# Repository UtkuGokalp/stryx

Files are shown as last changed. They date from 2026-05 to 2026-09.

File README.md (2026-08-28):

# Stryx

Stryx is a 3D printable wheeled robot designed as a platform for embedded software development. It has:
 - A power system that handles multiple power rails
 - An STM32 MCU (Nucleo L432KC) for controlling motors, sensors and potential future hardwares
 - An ultrasonic sensor for detecting obstacles
 - USB Connectivity
 - A modular platform that allows secure mounting
 - Various custom mounts

# Features
 - 3D printable parts (without supports)
 - Rear wheel drive via DC motors
 - Power system for managing different power rails
 - STM32 Nucleo L432KC MCU for real time control
 - Basic obstacle avoidance
 - DSP for removing sensor noises
 - Designed to be built on a mid-size breadboard for ease of prototyping and compactness
 - USB connectivity for universal communication (to be integrated better)

# Pictures
Below are the front, top and bottom views of Stryx.
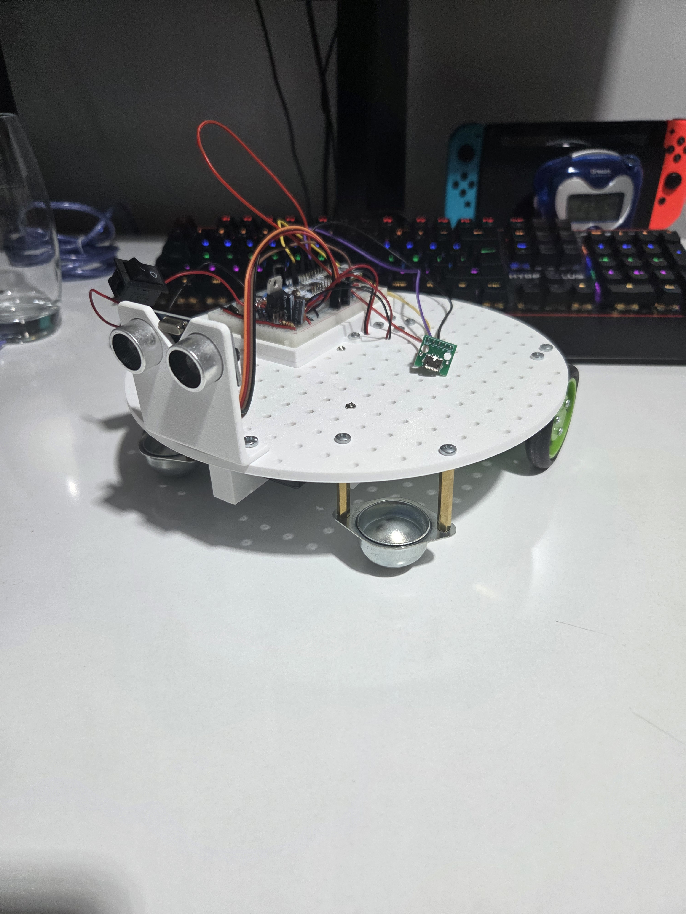
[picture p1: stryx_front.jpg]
Front view of Stryx v1


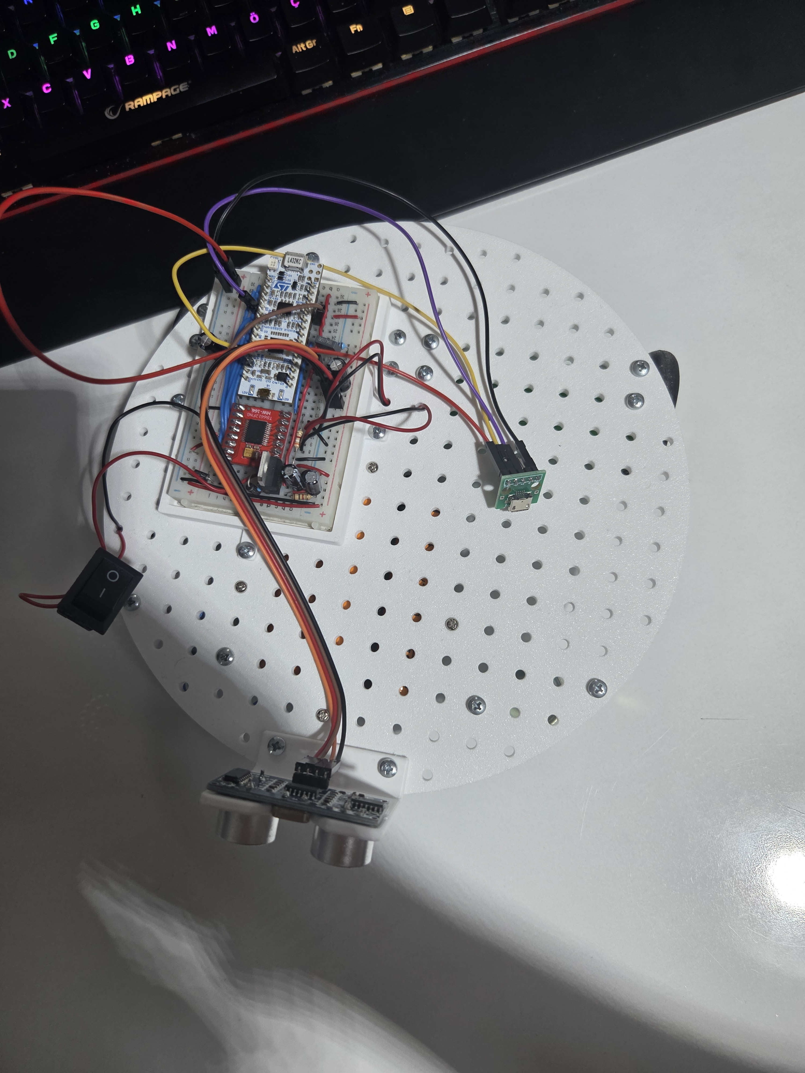
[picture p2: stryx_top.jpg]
Top view of Stryx v1


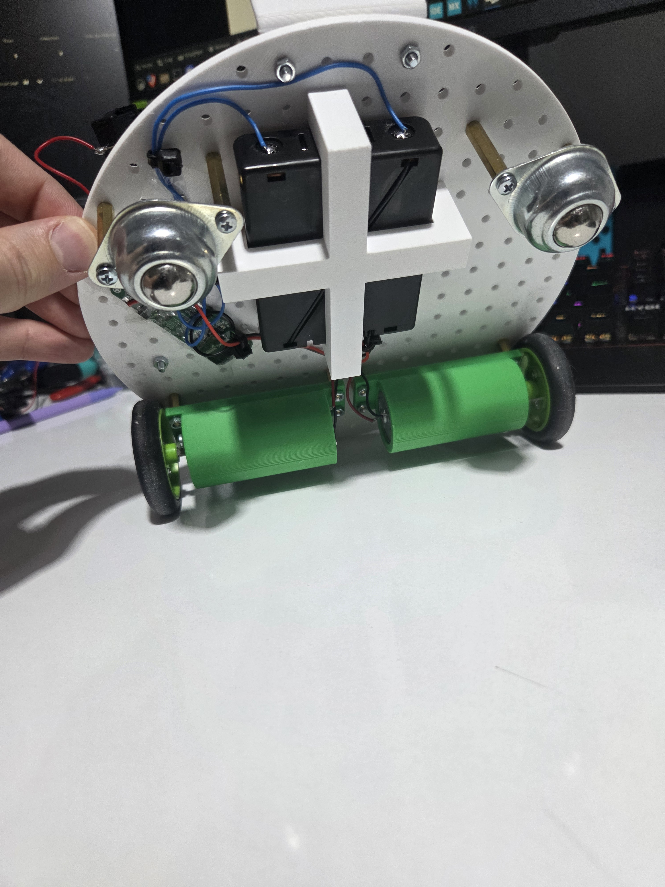
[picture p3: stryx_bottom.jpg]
Bottom view of Stryx v1


# Videos
  - A video of Stryx moving can be viewed [here](https://youtube.com/shorts/t5ViIWTwRgw?feature=share).
  - A video of Stryx detection through the ultrasonic sensor can be viewed [here](https://youtu.be/18g5bbReIh8).
 - Stryx being controlled by a custom controller and avoiding collisions can be viewed [here](https://youtube.com/shorts/JMSHhV6Dkls?si=vsp8z5HZcUrGIarE).

# Roadmap
Current plans to improve this project are in the following order:
 - PCB design
 - Better joystick controls
 - Better sensing of environment with either
   1. More sensors
   2. Servos that control the orientation of sensors
   3. Or sensors that use different technologies such as IR or LiDAR

# Parts List
|Name|Amount|
|-----|-----|
|Mid-size breadboard|1|
|STM32 Nucleo L432KC Dev Board|1|
|USB Micro-B breakout board|1|
|TB6612FNG Module|1|
|12V 250RPM DC Motors|2|
|Omnidirectional Wheels|2|
|LM317T Voltage regulator |1|
|1N4001|3|
|1N5822|1|
|0.1uF ceramic capacitor|2|
|1uF polarized capacitor|1|
|10uF polarized capacitor|1|
|470uF polarized capacitor|2|
|240Ω resistor|1|
|1kΩ resistor|2|
|3.8kΩ resistor|1|
|Neopixel LED Module|1|
|HC-SR04 ultrasonic sensor|1|
|3S 20A BMS|1|
|3200mAh Li-ion batteries|3|
|3S Li-ion battery holder|1|
|Switch (SPDT)|1|
|Screw Terminals|3|
|Rubber Wheels with D-Shaft connections|2|
|M3 screws, nuts, spacers and cables|various amounts|

# Schematic

Schematic is available in `kicad_files/` folder along with a PDF for quick viewing of the schematic.

Note: PDF may be outdated. KiCad project is the most up to date schematic.

# 3D Models

All 3D model files are in `3D_models/` folder along with printing instructions.

# How to build
## Mechanical
All parts are designed to align with the chassis mounting holes. Parts can be mounted wherever suitable, but keep in mind:
 - Wire lengths
 - Weight distribution and center of gravity
 - Accessibility

## Electronics
Components can be wired up according to the schematic in `kicad_files/`.

## Software
 1. Create a new STM32CubeIDE project using the `.ioc` file.
 2. Build the project.
 3. Connect the development board to the computer.
 4. Upload the firmware.

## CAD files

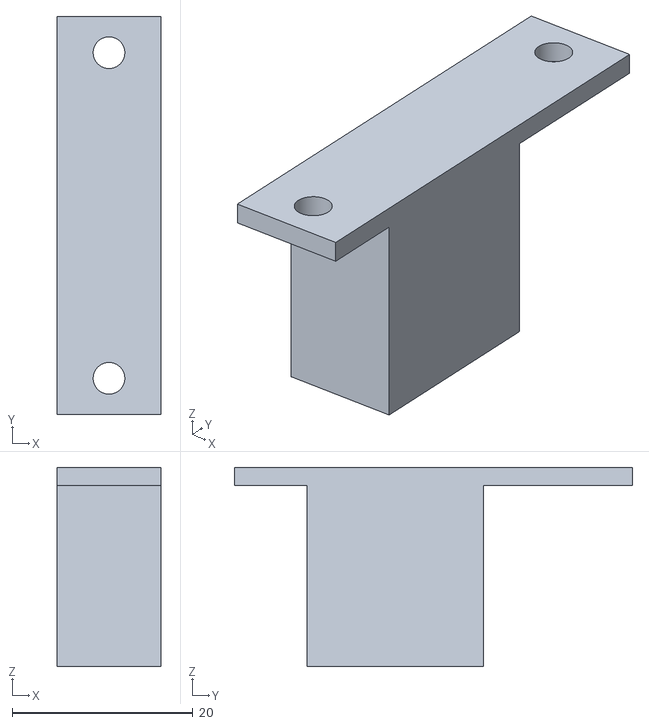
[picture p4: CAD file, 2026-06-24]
3D_models/nRF24L01 Holder.stl
11.5 x 44.0 x 22.0

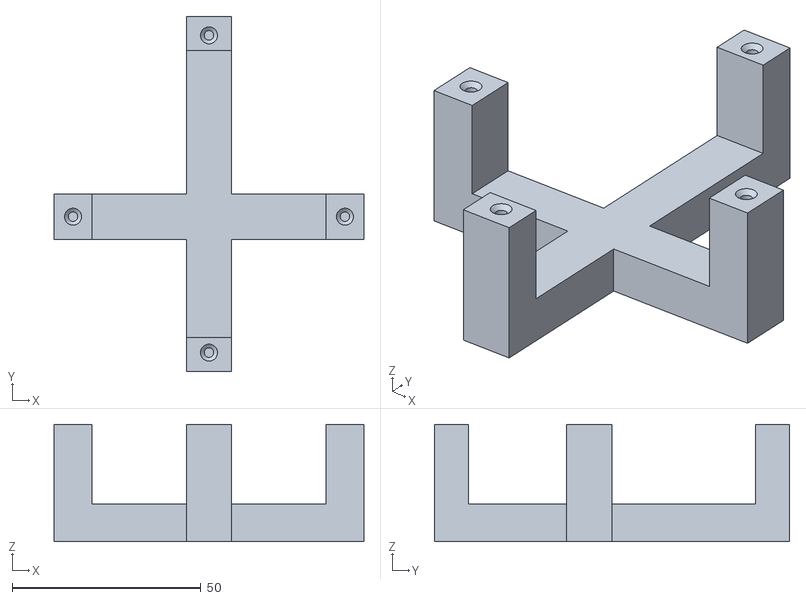
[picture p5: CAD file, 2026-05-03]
3D_models/3S 18650 Holder.stl
82.0 x 94.0 x 31.0

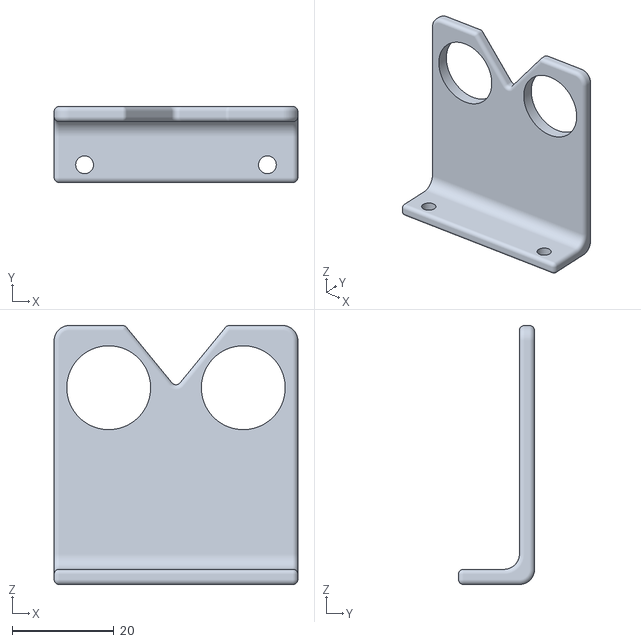
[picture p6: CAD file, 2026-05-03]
3D_models/HC-SR04 Holder.stl
48.0 x 15.0 x 51.0

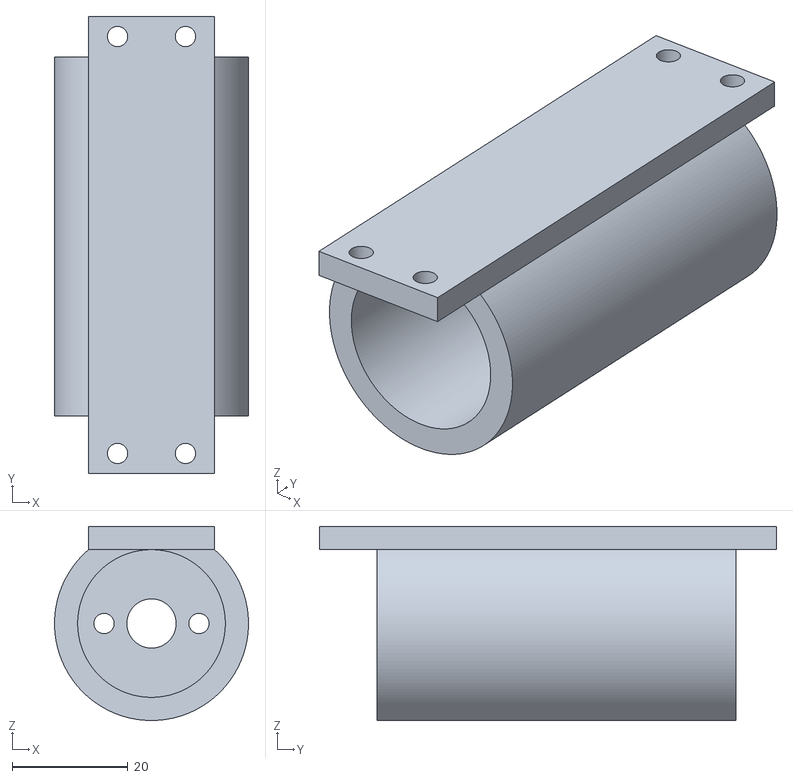
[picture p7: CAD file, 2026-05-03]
3D_models/25mm Motor Mount.stl
33.5 x 79.0 x 33.5

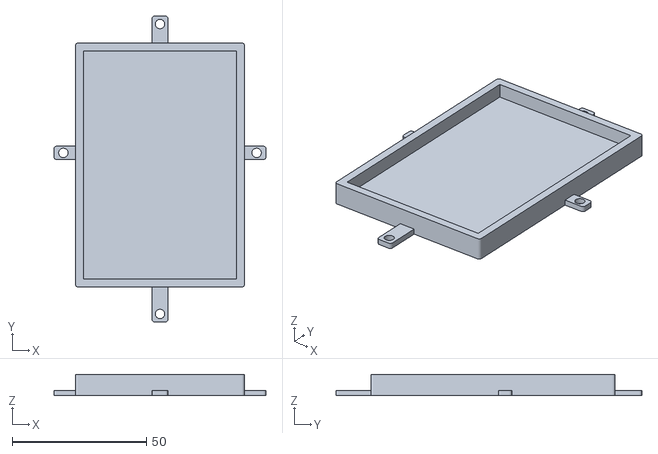
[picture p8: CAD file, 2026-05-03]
3D_models/Breadboard Holder.stl
79.0 x 114.0 x 8.00

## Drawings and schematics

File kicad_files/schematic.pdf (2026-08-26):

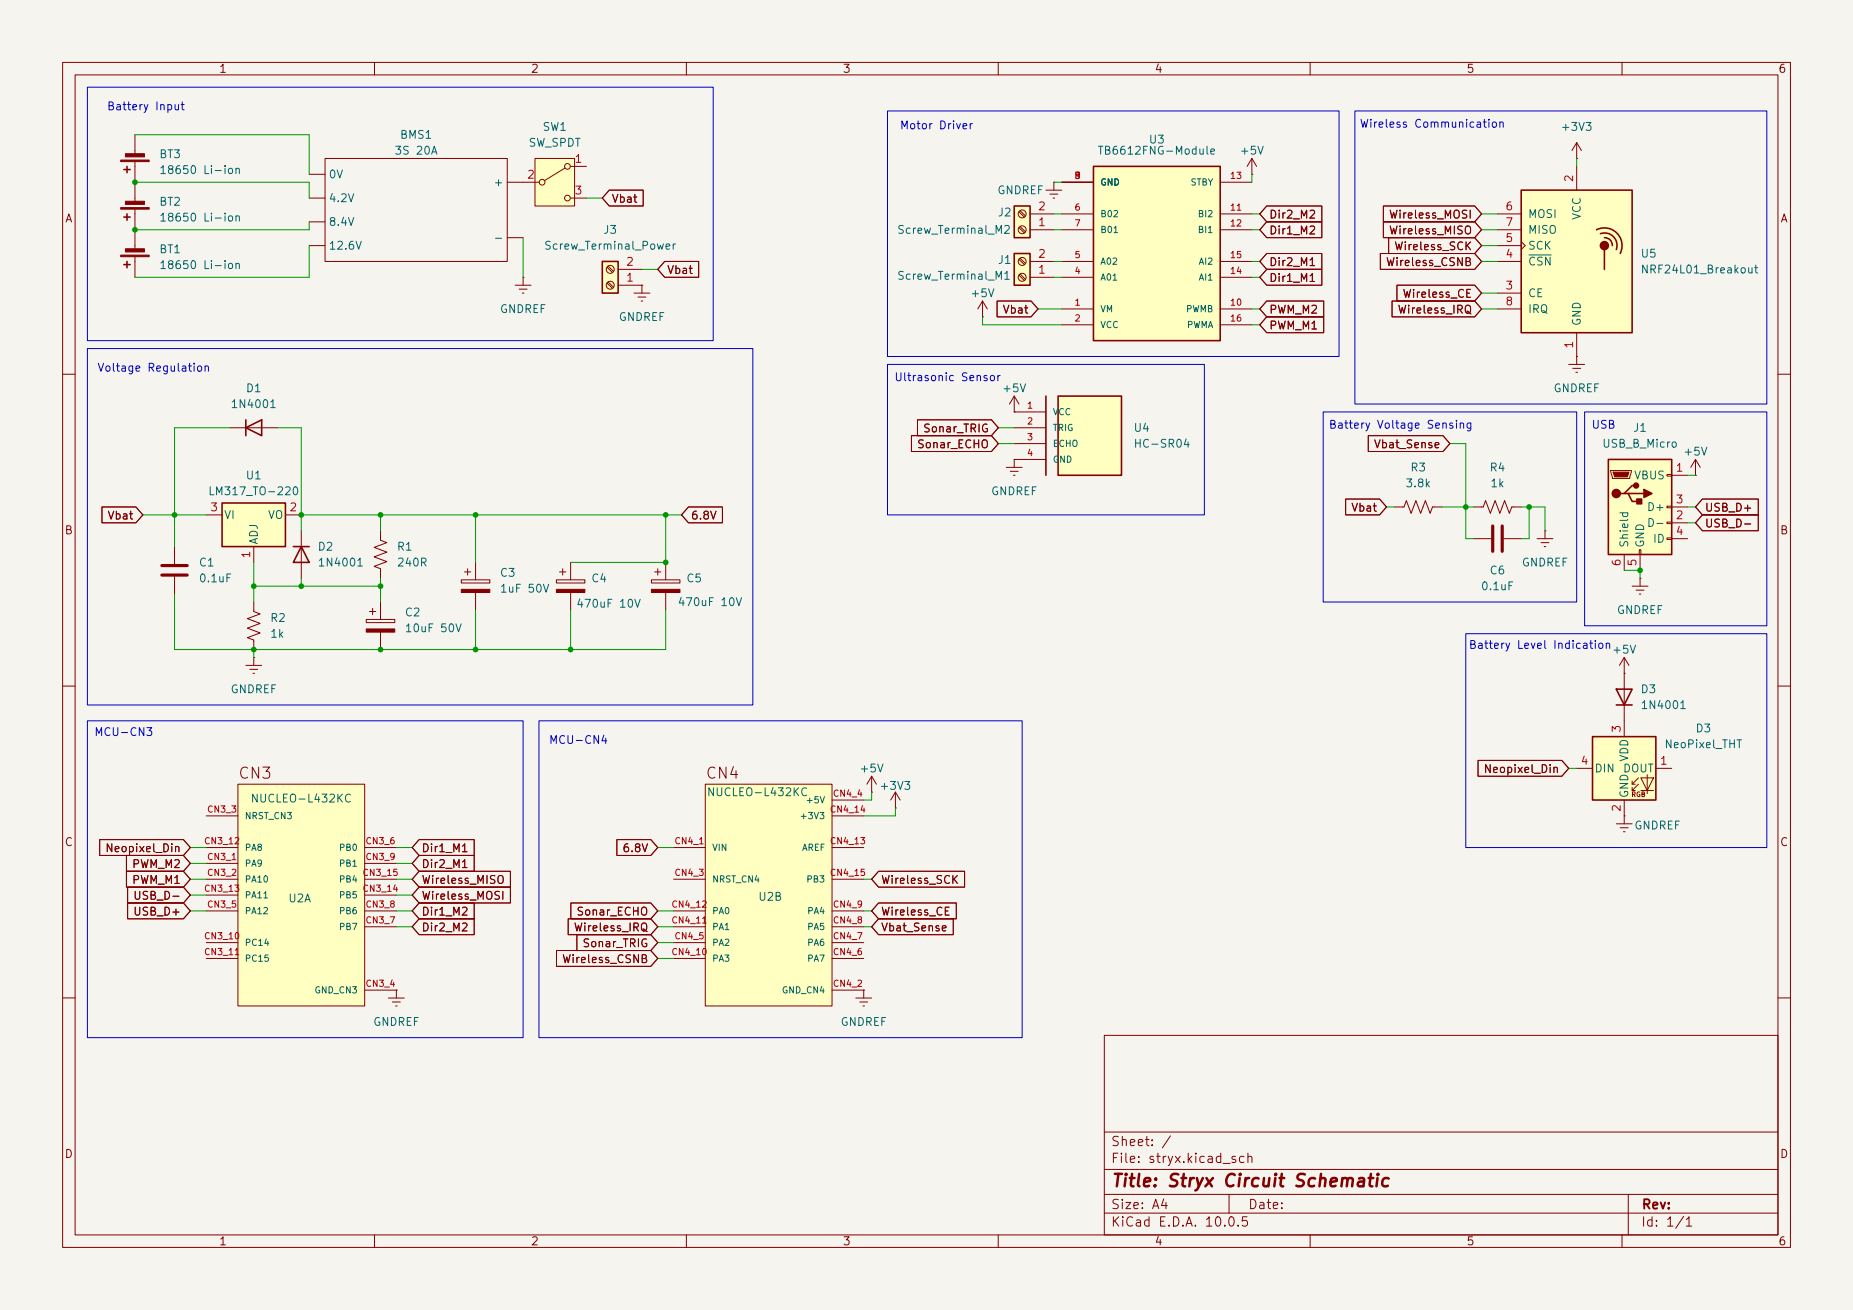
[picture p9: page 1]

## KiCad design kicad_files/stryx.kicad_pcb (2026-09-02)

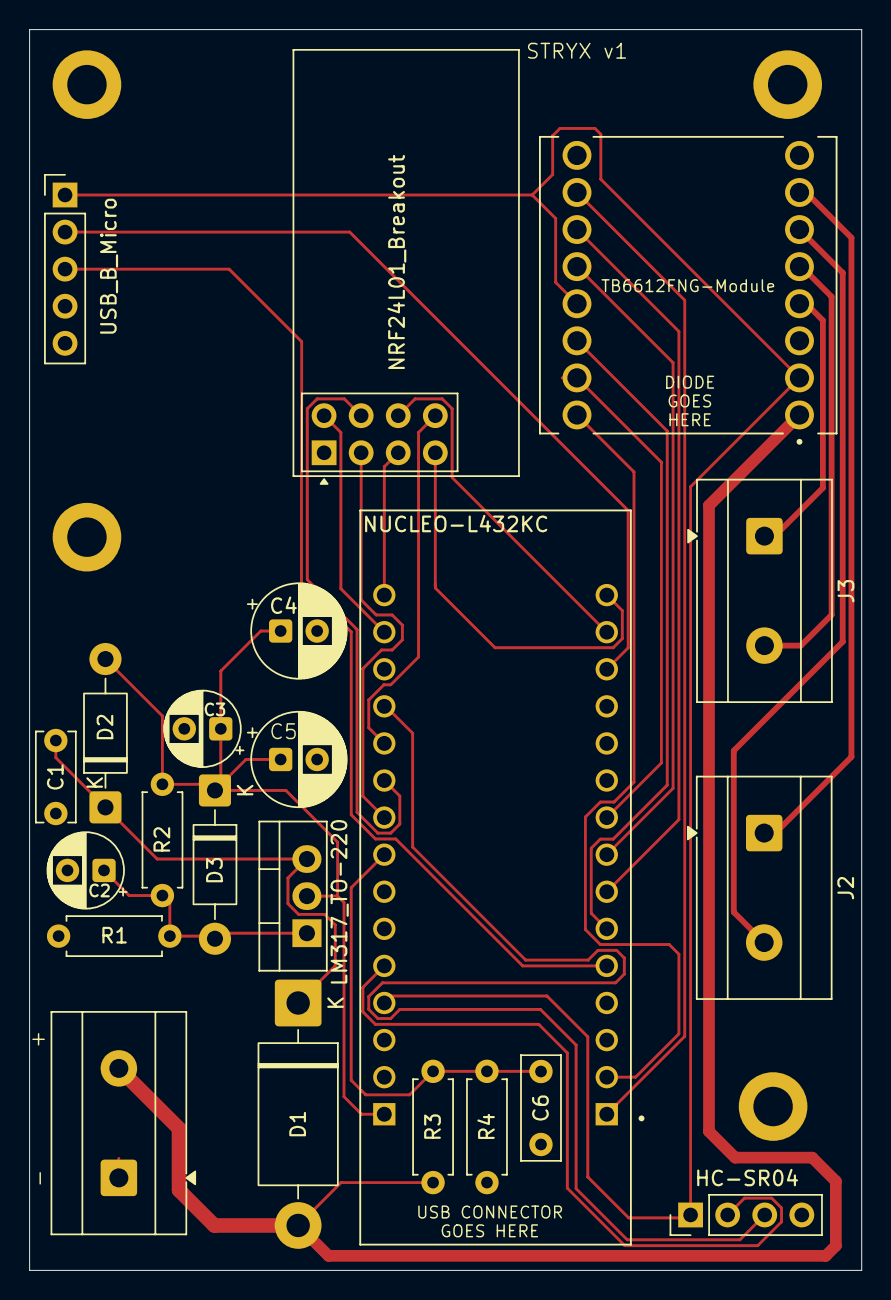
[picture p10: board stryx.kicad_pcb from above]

Board: 2 copper layers, 57.0 x 85.0 mm, 22 parts (0 on the bottom side), 28 nets.

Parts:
C1: 0.1uF; C_Disc_D6.0mm_W2.5mm_P5.00mm
C2: 10uF 50V; CP_Radial_D5.0mm_P2.50mm
C3: 1uF 50V; CP_Radial_D5.0mm_P2.50mm
C4, C5: 470uF 10V; CP_Radial_D6.3mm_P2.50mm
C6: 0.1uF; C_Rect_L7.0mm_W2.5mm_P5.00mm
D1: 1N5822; D_DO-201AD_P15.24mm_Horizontal
D2, D3: 1N4001; D_DO-41_SOD81_P10.16mm_Horizontal
J1: Screw_Terminal_Power; TerminalBlock_MetzConnect_Type171_RT13702HBWC_1x02_P7.50mm_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
J2: Screw_Terminal_M2; TerminalBlock_MetzConnect_Type171_RT13702HBWC_1x02_P7.50mm_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
J3: Screw_Terminal_M1; TerminalBlock_MetzConnect_Type171_RT13702HBWC_1x02_P7.50mm_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
J4: USB_B_Micro; PinHeader_1x05_P2.54mm_Vertical
R1, R4: 1k; R_Axial_DIN0207_L6.3mm_D2.5mm_P7.62mm_Horizontal
R2: 240R; R_Axial_DIN0207_L6.3mm_D2.5mm_P7.62mm_Horizontal
R3: 3.8k; R_Axial_DIN0207_L6.3mm_D2.5mm_P7.62mm_Horizontal
U1: LM317_TO-220; TO-220-3_Vertical
U2: NUCLEO-L432KC; MODULE_NUCLEO-L432KC
U3: HC-SR04; PinHeader_1x04_P2.54mm_Vertical
U4: TB6612FNG-Module; MODULE_ROB-14450
U5: NRF24L01_Breakout; nRF24L01_Breakout

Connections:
6.8V: C3.1, C4.1, C5.1, D2.2 (A), D3.1 (K), R2.1, U1.2 (VO), U2.CN4_1 (VIN)
+3V3: U2.CN4_14 (+3V3), U5.2 (VCC)
+5V: J4.1 (VBUS), U2.CN4_4 (+5V), U3.1 (VCC), U4.2 (VCC), U4.13 (STBY)
Dir1_M1: U2.CN3_6 (PB0), U4.14 (AI1)
Dir1_M2: U2.CN3_8 (PB6), U4.12 (BI1)
Dir2_M1: U2.CN3_9 (PB1), U4.15 (AI2)
Dir2_M2: U2.CN3_7 (PB7), U4.11 (BI2)
GNDREF: C1.1, C2.2, C3.2, C4.2, C5.2, C6.1, J1.1, J4.5 (GND), R1.2, R4.2, U2.CN3_4 (GND_CN3), U2.CN4_2 (GND_CN4), U3.4 (GND), U4.3 (GND), U4.8 (GND), U4.9 (GND), U5.1 (GND)
unnamed: C1.2, D1.1 (K), D2.1 (K), U1.3 (VI)
unnamed: C2.1, D3.2 (A), R1.1, R2.2, U1.1 (ADJ)
unnamed: J2.1, U4.7 (B01)
unnamed: J2.2, U4.6 (B02)
unnamed: J3.1, U4.4 (A01)
unnamed: J3.2, U4.5 (A02)
PWM_M1: U2.CN3_2 (PA10), U4.16 (PWMA)
PWM_M2: U2.CN3_1 (PA9), U4.10 (PWMB)
Sonar_ECHO: U2.CN4_12 (PA0), U3.3 (ECHO)
Sonar_TRIG: U2.CN4_5 (PA2), U3.2 (TRIG)
USB_D+: J4.3 (D+), U2.CN3_5 (PA12)
USB_D-: J4.2 (D-), U2.CN3_13 (PA11)
Vbat: D1.2 (A), J1.2, R3.1, U4.1 (VM)
Vbat_Sense: C6.2, R3.2, R4.1, U2.CN4_8 (PA5)
Wireless_CE: U2.CN4_9 (PA4), U5.3 (CE)
Wireless_CSNB: U2.CN4_10 (PA3), U5.4 (~CSN)
Wireless_IRQ: U2.CN4_11 (PA1), U5.8 (IRQ)
Wireless_MISO: U2.CN3_15 (PB4), U5.7 (MISO)
Wireless_MOSI: U2.CN3_14 (PB5), U5.6 (MOSI)
Wireless_SCK: U2.CN4_15 (PB3), U5.5 (SCK)

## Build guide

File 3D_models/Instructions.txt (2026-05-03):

All of the parts were printed using eSun Basic White PLA with default settings of BambuStudio slicer software on a Bambu Lab P1S. You shouldn't need any supports as long as you orient the models correctly.

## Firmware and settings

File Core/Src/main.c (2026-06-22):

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
/* Includes ------------------------------------------------------------------*/
#include "main.h"
#include "usb_device.h"

/* USER CODE BEGIN Includes */
#include "robot.h"
/* USER CODE END Includes */

ADC_HandleTypeDef hadc1;
DMA_HandleTypeDef hdma_adc1;

SPI_HandleTypeDef hspi3;

TIM_HandleTypeDef htim1;
TIM_HandleTypeDef htim2;
TIM_HandleTypeDef htim6;
TIM_HandleTypeDef htim7;
TIM_HandleTypeDef htim15;
DMA_HandleTypeDef hdma_tim1_ch1;

void SystemClock_Config(void);
void PeriphCommonClock_Config(void);
static void MX_GPIO_Init(void);
static void MX_DMA_Init(void);
static void MX_ADC1_Init(void);
static void MX_TIM1_Init(void);
static void MX_TIM7_Init(void);
static void MX_TIM6_Init(void);
static void MX_TIM15_Init(void);
static void MX_TIM2_Init(void);
static void MX_SPI3_Init(void);
/* USER CODE BEGIN 0 */
//This function retargets the stdout to the USB peripheral
//so that printf will work normally (except it needs to be
//viewed from a serial terminal).
#include "usbd_cdc_if.h"
int _write(int file, char* ptr, int len)
{
	CDC_Transmit_FS((uint8_t*)ptr, len);
	return len;
}
/* USER CODE END 0 */

/**
  * @brief  The application entry point.
  * @retval int
  */
int main(void)
{

  /* MCU Configuration--------------------------------------------------------*/

  /* Reset of all peripherals, Initializes the Flash interface and the Systick. */
  HAL_Init();

  /* Configure the system clock */
  SystemClock_Config();

  /* Configure the peripherals common clocks */
  PeriphCommonClock_Config();

  /* Initialize all configured peripherals */
  MX_GPIO_Init();
  MX_DMA_Init();
  MX_ADC1_Init();
  MX_TIM1_Init();
  MX_TIM7_Init();
  MX_TIM6_Init();
  MX_TIM15_Init();
  MX_TIM2_Init();
  MX_USB_DEVICE_Init();
  MX_SPI3_Init();
  /* Infinite loop */
  /* USER CODE BEGIN WHILE */
  //This is the actual main loop, the while(1) loop below is not used as the main loop.
  robot_main();
  while (1)
  {
    /* USER CODE END WHILE */

    /* USER CODE BEGIN 3 */
  }
  /* USER CODE END 3 */
}

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


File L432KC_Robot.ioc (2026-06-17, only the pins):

Mcu.UserName=STM32L432KCUx
PA0.GPIO_Label=HCSR04_Echo
PA0.Signal=S_TIM2_CH1
PA1.GPIO_Label=nRF24L01_IRQ
PA1.Signal=GPIO_Input
PA10.GPIO_Label=MotorA_PWM
PA10.Signal=S_TIM1_CH3
PA11.Signal=USB_DM
PA12.Signal=USB_DP
PA2.GPIO_Label=HCSR04_Trig
PA2.Signal=S_TIM15_CH1
PA3.GPIO_Label=nRF24L01_CSN
PA3.Signal=GPIO_Output
PA4.GPIO_Label=nRF24L01_CE
PA4.Signal=GPIO_Output
PA5.GPIO_Label=BAT_SENSE
PA5.Signal=ADCx_IN10
PA8.GPIO_Label=NeoPixel_PWM
PA8.Signal=S_TIM1_CH1
PA9.GPIO_Label=MotorB_PWM
PA9.Signal=S_TIM1_CH2
PB0.GPIO_Label=MotorA_In1
PB0.Signal=GPIO_Output
PB1.GPIO_Label=MotorA_In2
PB1.Signal=GPIO_Output
PB5.Signal=SPI3_MOSI
PB6.GPIO_Label=MotorB_In1
PB6.Signal=GPIO_Output
PB7.GPIO_Label=MotorB_In2
PB7.Signal=GPIO_Output

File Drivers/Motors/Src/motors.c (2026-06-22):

/*
 * motors.c
 *
 *  Created on: Apr 27, 2026
 *      Author: ugklp
 */

#include "motors.h"
#include "main.h"
#include "utils.h"

extern TIM_HandleTypeDef htim1;

void InitMotors(void)
{
	StopMotor(MOTOR_A | MOTOR_B); //Ensure the GPIO is set to that the motors will start stopped.
	SetMotorSpeed(MOTOR_A | MOTOR_B, 0, true); //Ensure the PWM duty cycles are set to 0 before starting the timers.
	HAL_TIM_PWM_Start(&htim1, TIM_CHANNEL_3);
	HAL_TIM_PWM_Start(&htim1, TIM_CHANNEL_2);
}

void StopMotor(MOTOR motor)
{
	/*
	  To perform stop operation, the PWM signal needs to be left high (100% duty cycle).
	*/
	if (motor == MOTOR_A)
	{
		HAL_GPIO_WritePin(MotorA_In1_GPIO_Port, MotorA_In1_Pin, GPIO_PIN_RESET);
		HAL_GPIO_WritePin(MotorA_In2_GPIO_Port, MotorA_In2_Pin, GPIO_PIN_RESET);
		__HAL_TIM_SET_COMPARE(&htim1, TIM_CHANNEL_3, htim1.Instance->ARR + 1); //Leave PWM at 100% duty cycle (PWM Mode 1)
	}
	else if (motor == MOTOR_B)
	{
		HAL_GPIO_WritePin(MotorB_In1_GPIO_Port, MotorB_In1_Pin, GPIO_PIN_RESET);
		HAL_GPIO_WritePin(MotorB_In2_GPIO_Port, MotorB_In2_Pin, GPIO_PIN_RESET);
		__HAL_TIM_SET_COMPARE(&htim1, TIM_CHANNEL_2, htim1.Instance->ARR + 1);//Leave PWM at 100% duty cycle (PWM Mode 1)
	}
	else if (motor == (MOTOR_A | MOTOR_B))
	{
		StopMotor(MOTOR_A);
		StopMotor(MOTOR_B);
	}
}

void BrakeMotor(MOTOR motor)
{
	/*
	 Both inputs being high is the only option that performs a short brake regardless of the PWM signal.
	 Implementing this as the brake function also allows us to leave PWM signal alone in this function.
	*/
	if (motor == MOTOR_A)
	{
		HAL_GPIO_WritePin(MotorA_In1_GPIO_Port, MotorA_In1_Pin, GPIO_PIN_SET);
		HAL_GPIO_WritePin(MotorA_In2_GPIO_Port, MotorA_In2_Pin, GPIO_PIN_SET);
	}
	else if (motor == MOTOR_B)
	{
		HAL_GPIO_WritePin(MotorB_In1_GPIO_Port, MotorB_In1_Pin, GPIO_PIN_SET);
		HAL_GPIO_WritePin(MotorB_In2_GPIO_Port, MotorB_In2_Pin, GPIO_PIN_SET);
	}
	else if (motor == (MOTOR_A | MOTOR_B))
	{
		BrakeMotor(MOTOR_A);
		BrakeMotor(MOTOR_B);
	}
}

void SetMotorDirection(MOTOR motor, bool forward)
{
	if (forward)
	{
		SetMotorDirection_CW(motor);
	}
	else
	{
		SetMotorDirection_CCW(motor);
	}
}

void SetMotorDirection_CCW(MOTOR motor)
{
	if (motor == MOTOR_A)
	{
		HAL_GPIO_WritePin(MotorA_In1_GPIO_Port, MotorA_In1_Pin, GPIO_PIN_RESET);
		HAL_GPIO_WritePin(MotorA_In2_GPIO_Port, MotorA_In2_Pin, GPIO_PIN_SET);
	}
	else if (motor == MOTOR_B)
	{
		HAL_GPIO_WritePin(MotorB_In1_GPIO_Port, MotorB_In1_Pin, GPIO_PIN_RESET);
		HAL_GPIO_WritePin(MotorB_In2_GPIO_Port, MotorB_In2_Pin, GPIO_PIN_SET);
	}
	else if (motor == (MOTOR_A | MOTOR_B))
	{
		SetMotorDirection_CCW(MOTOR_A);
		SetMotorDirection_CCW(MOTOR_B);
	}
}

void SetMotorDirection_CW(MOTOR motor)
{
	if (motor == MOTOR_A)
	{
		HAL_GPIO_WritePin(MotorA_In1_GPIO_Port, MotorA_In1_Pin, GPIO_PIN_SET);
		HAL_GPIO_WritePin(MotorA_In2_GPIO_Port, MotorA_In2_Pin, GPIO_PIN_RESET);
	}
	else if (motor == MOTOR_B)
	{
		HAL_GPIO_WritePin(MotorB_In1_GPIO_Port, MotorB_In1_Pin, GPIO_PIN_SET);
		HAL_GPIO_WritePin(MotorB_In2_GPIO_Port, MotorB_In2_Pin, GPIO_PIN_RESET);
	}
	else if (motor == (MOTOR_A | MOTOR_B))
	{
		SetMotorDirection_CW(MOTOR_A);
		SetMotorDirection_CW(MOTOR_B);
	}
}

void SetMotorSpeed(MOTOR motor, uint8_t speed, bool forward)
{
	//The direction needs to be set first in order to make
	//sure the motors are set to moving and not stopping
	SetMotorDirection(motor, forward);

	uint32_t ccr = map(speed, 0, 255, 0, htim1.Instance->ARR + 1);
	if (motor == MOTOR_A)
	{
		__HAL_TIM_SET_COMPARE(&htim1, TIM_CHANNEL_3, ccr);
	}
	else if (motor == MOTOR_B)
	{
		__HAL_TIM_SET_COMPARE(&htim1, TIM_CHANNEL_2, ccr);
	}
	else if (motor == (MOTOR_A | MOTOR_B))
	{
		SetMotorSpeed(MOTOR_A, speed, forward);
		SetMotorSpeed(MOTOR_B, speed, forward);
	}
}

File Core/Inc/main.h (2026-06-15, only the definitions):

#define HCSR04_Echo_Pin GPIO_PIN_0
#define HCSR04_Echo_GPIO_Port GPIOA
#define nRF24L01_IRQ_Pin GPIO_PIN_1
#define nRF24L01_IRQ_GPIO_Port GPIOA
#define HCSR04_Trig_Pin GPIO_PIN_2
#define HCSR04_Trig_GPIO_Port GPIOA
#define nRF24L01_CSN_Pin GPIO_PIN_3
#define nRF24L01_CSN_GPIO_Port GPIOA
#define nRF24L01_CE_Pin GPIO_PIN_4
#define nRF24L01_CE_GPIO_Port GPIOA
#define BAT_SENSE_Pin GPIO_PIN_5
#define BAT_SENSE_GPIO_Port GPIOA
#define MotorA_In1_Pin GPIO_PIN_0
#define MotorA_In1_GPIO_Port GPIOB
#define MotorA_In2_Pin GPIO_PIN_1
#define MotorA_In2_GPIO_Port GPIOB
#define NeoPixel_PWM_Pin GPIO_PIN_8
#define NeoPixel_PWM_GPIO_Port GPIOA
#define MotorB_PWM_Pin GPIO_PIN_9
#define MotorB_PWM_GPIO_Port GPIOA
#define MotorA_PWM_Pin GPIO_PIN_10
#define MotorA_PWM_GPIO_Port GPIOA
#define MotorB_In1_Pin GPIO_PIN_6
#define MotorB_In1_GPIO_Port GPIOB
#define MotorB_In2_Pin GPIO_PIN_7
#define MotorB_In2_GPIO_Port GPIOB

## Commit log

2026-05-03 Added the schematic as a pdf file
2026-05-03 Updated 3D printing instructions
2026-05-03 Updated schematic and deleted auto-generated backups. A future commit will disable tracking of backups
    [stryx.kicad_sch]
2026-05-03 Updated .gitignore to not track kicad backups and lock files
2026-05-05 Updated schematic to include USB connectivity
    [stryx.kicad_sch]
2026-05-05 Add USB Micro-B breakout board to components list
2026-05-07 Analyzed the sensor data, designed a proper filter, removed unnecesary timer usage and fixed issues with reading sensor data
    [HCSR04.c, L432KC_Robot.ioc, main.c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]
2026-05-07 Update README with video links for Stryx
    Added links to videos demonstrating Stryx's movement and ultrasonic detection.
2026-06-13 fixed interrupt mess by using HAL interrupt callback system
    [HCSR04.c, L432KC_Robot.ioc, batt_mon.c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]
2026-06-14 Generated STM32 SPI HAL for implementing nRF24L01 driver
2026-06-14 Fixed SPI configuration on CubeMX
    [L432KC_Robot.ioc, main.c]
2026-06-15 Implemented the SPI communication and reading register for nRF24L01
2026-06-17 Completed the nRF24L01 driver for receiving signals
2026-06-22 Fixed a bug with the TB6612FNG driver code and started experimentations for joystick controls
    [joystick.c, motors.c, nRF24L01.c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]
2026-06-22 Redirected printf to USB and fixed function calling bug.
    [joystick.c, main.c]
2026-06-24 Added the design file for nRF24L01 mount
    [nRF24L01 Holder.stl]
2026-06-24 Updated schematic
    [stryx.kicad_sch]

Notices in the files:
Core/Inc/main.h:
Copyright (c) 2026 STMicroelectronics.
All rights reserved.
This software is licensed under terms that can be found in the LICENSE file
